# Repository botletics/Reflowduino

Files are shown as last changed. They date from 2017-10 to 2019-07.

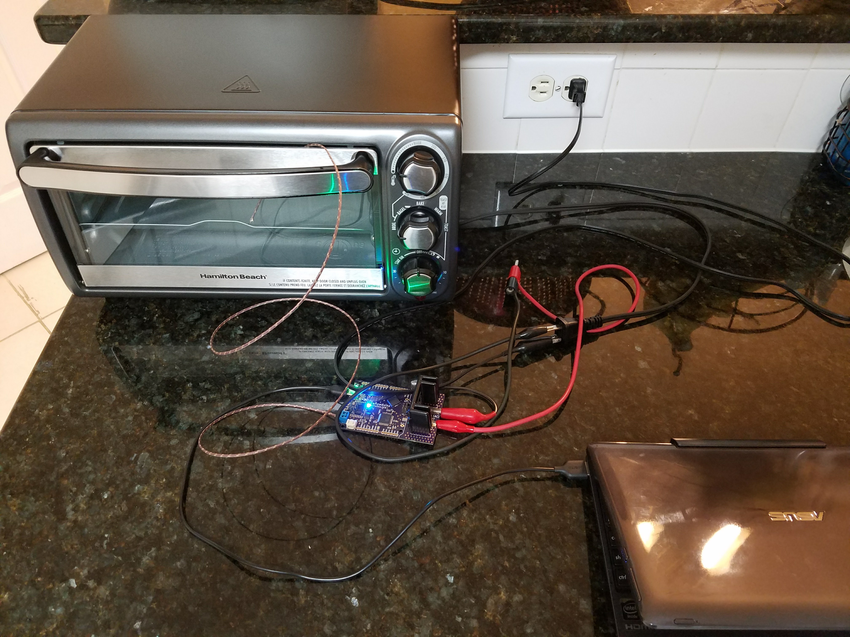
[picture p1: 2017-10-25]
Media/Toaster Oven Test Setup 1.jpg

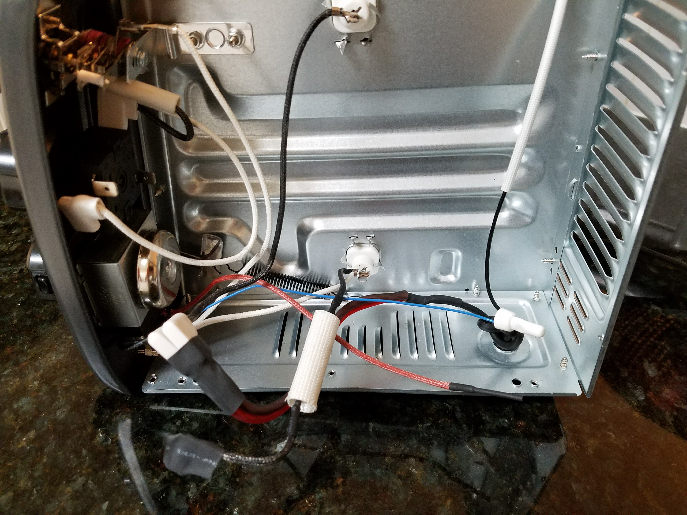
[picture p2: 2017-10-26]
Media/Toaster Oven Finished Wiring.jpg

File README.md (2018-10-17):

# Reflowduino

## Introduction
First off, let's briefly explain a circuit board is assembled. To aid in the explanation, let's take the analogy of baking a pizza. First of all you'll need the crust, which for us is a bare printed circuit board (PCB) made with different layers of a plastic substrate and copper traces that make the electrical connections. Next, we'll need the cheese that holds everything together, which for us is solder paste (yes, solder in the form of a paste) which "reflows" (solidifies or cures) at a high temperature. The solder paste is applied to the exposed copper pads on the PCB by way of a stencil that is aligned over the PCB. Then we'll grab some toppings, the electrical components, and place them in their appropriate locations on top of the solder paste. The final step is to bake our "pizza" so that the "cheese" holds all the components in place to yield our final assembled board! This is where the Reflowduino project comes in...

## Overview
The Reflowduino project is an entire do-it-yourself (DIY) reflow ecosystem consisting of open-source hardware specifically built to make it easy to control reflow appliances and apply PID temperature control while maintaining full flexibility in programming and usage while offering a bunch of features.

Since I'm a firm believer of great online resources having learned everything on my own aside from my Mechanical Engineering degree, I'm sharing all of this as completely open-source for everyone to enjoy, including EAGLE PCB files, Arduino IDE example code, sample Android app for Bluetooth control, and full tutorials on how to modify a toaster oven to start cookin’!

That being said, I do offer the boards listed below [for sale on my website](https://www.botletics.com/products/). Each order helps me out a little bit in creating and sharing new projects with everyone! :)

## Resources
Don’t forget to check out the [comprehensive Github wiki](https://github.com/botletics/Reflowdiuno/wiki)!
I also posted [this Instructable](https://www.instructables.com/id/Reflowduino-DIY-BLE-Reflow-Oven-Controller/) as a quick 'n dirty summary of everything here as well as on [Hackster.io](https://www.hackster.io/botletics/diy-reflow-oven-with-reflowduino-af0219)!

All PCB design files and hardware are released under the [Creative Commons Attribution Share Alike 4.0](https://choosealicense.com/licenses/cc-by-sa-4.0/) license.

All other software is released under the [GNU General Public License v3.0](https://choosealicense.com/licenses/gpl-3.0/).

## Safety Disclaimer
If you are a beginner in electronics or don't have the proper experience to work with mains voltage, I would suggest that you either don't mess with it, consult a professional, or keep learning until you're proficient enough! I am not liable for any mishaps that may occur due to misuse of the Reflowduino or its associated components or electrical system (including mains power). Take all safety precautions as necessary, such as gloves and certified safety glasses. Moreover, it is not recommended that you use the same appliance to reflow PCB's and also to cook food for consumption, which may result in food poisoning, especially with leaded solder. You are fully responsible for your actions, and perform them at your own risk!

That being said, DIY away my friends... have fun and stay safe!

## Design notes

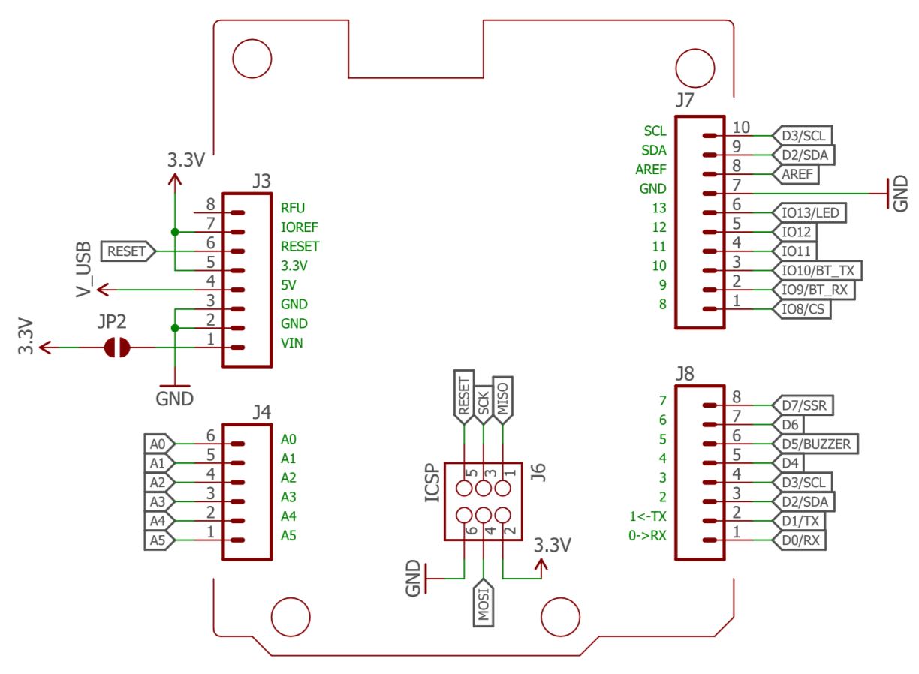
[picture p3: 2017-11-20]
Media/SchematicPinout.JPG

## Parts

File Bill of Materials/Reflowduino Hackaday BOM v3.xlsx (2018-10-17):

Part # | Part Description | Quantity | Notes | Mfg. Number
C1, C5 | 4.7uF/6.3V/10%/X5R Ceramic Capacitor 0603 | 2 |  | CL10A475KQ8NNNL
C2,C4,C8,C10 | 0.1uF/16V/20%/X7R Ceramic Capacitor 0603 | 4 |  | CL10B104MO8NNND
C3, C6, C7 | 1uF/25V/10%/X5R Ceramic Capacitor, 0603 | 3 |  | CL10A105KA8NNLC
C9 | 0.01uF/16V/10%/X7R Ceramic Capacitor 0603 | 1 |  | CL10B103KO8NNNC
D1 | Schottky Diode, 20V/1A, SOD-123FL | 1 |  | MBR120VLSFT3G
F1 | PTC Resettable Fuse, 750mA | 1 | 1210 package | 0ZCH0075AF2E
IC1 | Single Cell Li-Ion Charger IC, SOT23-5 | 1 |  | MCP73831T-2ACIOT
IC2 | ATMEGA32U4RC-AU, 44TQFP (10x10) | 1 | Internal calib. RC | ATMEGA32U4RC-AU
IC3 | 3.3V/600mA Regulator, SOT23-5 | 1 |  | AP2112K-3.3TRG1
IC4 | MAX31855 Thermocouple-to-Digital Converter | 1 | K-type | MAX31855KASA+
J1 | Micro USB Connector, SMT with Alignment Pins | 1
J2 | 2mm JST-PH SMT RA Connector | 1 |  | S2B-PH-SM4-TB(LF)(SN)
J3, J8 | 1x8 Female Header, 2.54mm Pitch/8.5mm Tall | 2
J4 | 1x6 Female Header, 2.54mm Pitch/8.5mm Tall | 1
J5 | 2-pin Screw Terminal Block, 3.5mm Pitch | 1 |  | T502015000J0G
J6 | 3x2 ICSP Male Header, 2.54mm Pitch | 1 |  | 54102-G08-00
J7 | 10x1 Female Header, 2.54mm Pitch/8.5mm Tall | 1
L1-L2 | 600Ohm Ferrite Bead, Signal Filter, 0603 | 2 |  | BLM18TG601TN1D
LED1-LED2 | 3.2V/20mA Green LED, 0603 | 2 |  | 150060GS75000
LED3 | 2V/20mA Red LED, 0603 | 1 |  | 150060RS75000
LED4 | 3.2V/20mA Blue LED, 0603 | 1 |  | 150060BS75000
Q1 | N-MOSFET, 200mA, SOT23-3 | 1 | Very low Vth | BSS138L
R1, R3 | 2k/1%/0.1W Resistor 0603 | 2 |  | ERJ-3GEYJ202V
R2, R4 | 22/5%/0.1W Resistor 0603 | 2 |  | RC1608J220CS
R5,R9,R10 | 10k/5%/0.1W Resistor 0603 | 3 |  | NRC06J103TRF
R6-R7 | 4.02k/1%/0.1W Resistor 0603 | 2 |  | RK73H1JTTD4021F
R8, R11 | 470/5%/0.1W Resistor 0603 | 2 |  | RMCF0603JT470R
RY1 | Opto-Isolated Solid State Relay | 1 | 25A/280V max | SPF240D25
SPK1 | Piezo Buzzer, 65dB | 1 |  | PKMCS0909E4000-R1
SW1 | Pushbutton Switch, SPST-NO, 300gf/2.5mm Tall | 1 |  | KMR731NGLFS
U1 | HM-11 Bluetooth SMD Module | 1
Y1 | 8MHz Resonator | 1 |  | CSTCE8M00G52-R0
 | K-type Thermocouple, Glass Braid Insulation | 1 |  | 240-080

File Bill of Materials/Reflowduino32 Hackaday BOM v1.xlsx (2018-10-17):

Part # | Part Name | Quantity | Notes | Mfg. Number
C1 | 0.1uF/16V/20%/X7R Ceramic Capacitor 0603 | 1 |  | CL10B104MO8NNND
C2 | 0.01uF/16V/10%/X7R Ceramic Capacitor 0603 | 1 |  | CL10B103KO8NNNC
IC1 | MAX31855 Thermocouple-to-Digital Converter | 1 | K-type | MAX31855KASA+
J1, J3 | 1x6 Female Header, 2.54mm Pitch/8.5mm Tall | 2
J5-J6 | 2-pin Screw Terminal Block, 3.5mm Pitch | 2 |  | T502015000J0G
L1-L2 | 600Ohm Ferrite Bead, Signal Filter, 0603 | 2 |  | BLM18TG601TN1D
Q1 | N-MOSFET, 200mA, SOT23-3 | 1 | Very low Vth | BSS138L
R1-R2 | 10k/5%/0.1W Resistor 0603 | 2 |  | NRC06J103TRF

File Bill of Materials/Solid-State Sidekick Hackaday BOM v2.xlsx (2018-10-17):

Part # | Part Description | Quantity | Notes | Mfr. Number
J1 | C14 Entry Conn Receptacle, Right Angle | 1 |  | 703W-00/53
J2 | AC Receptacle | 1 |  | 3-213598-2
J3 | 2-pin Screw Terminal Block, 3.5mm Pitch | 1 |  | T502015000J0G
RY1 | Opto-Isolated Solid State Relay | 1 | 25A/280V max | SPF240D25
SW1 | SPST ON-OFF Rocker Switch, Right Angle | 1 | 15A/125VAC | R1966ABLKBLKFR

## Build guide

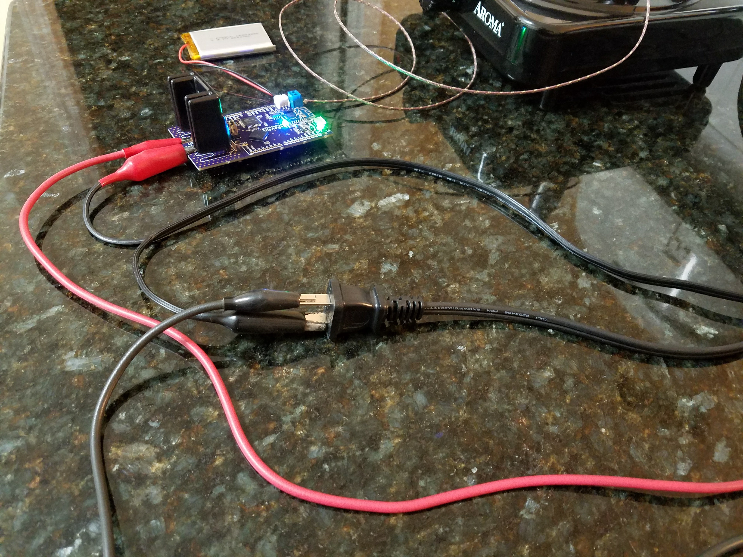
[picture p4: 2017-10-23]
Media/Hot Plate Demo Setup Closeup.jpg

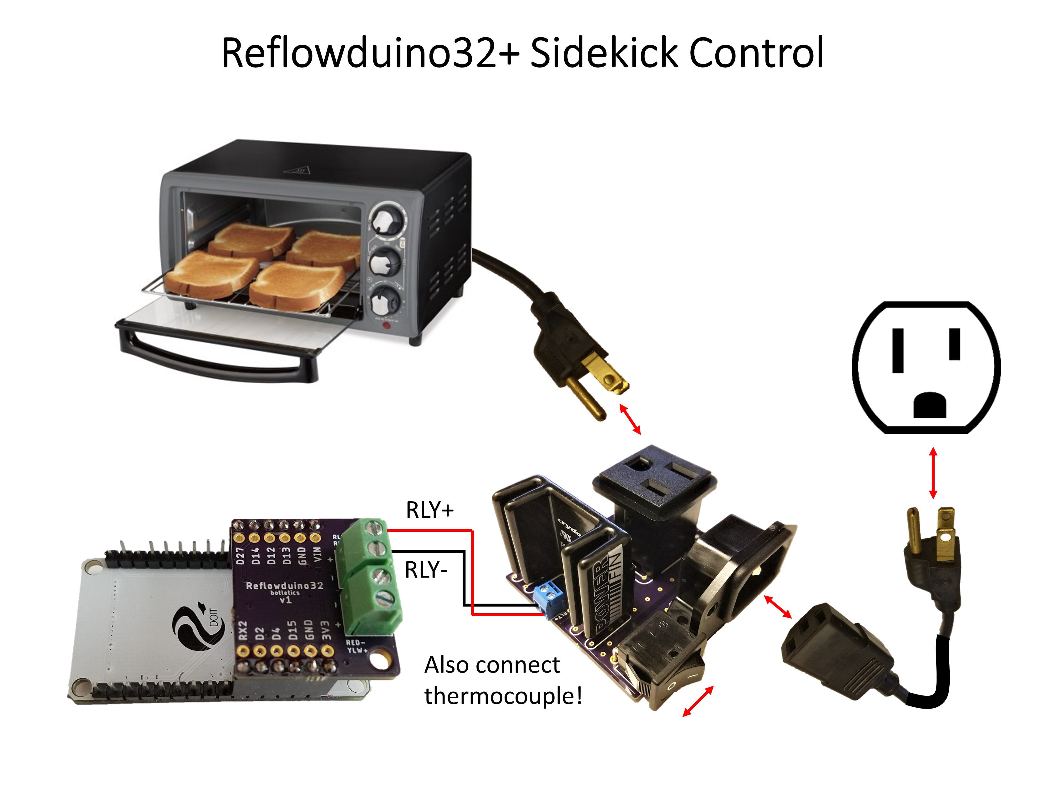
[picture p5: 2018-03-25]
Media/Reflowduino32 + Sidekick Wiring.jpg

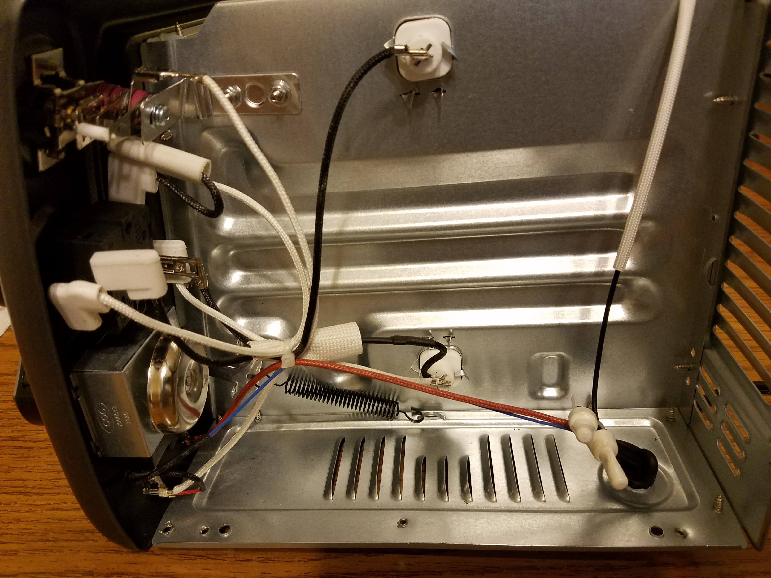
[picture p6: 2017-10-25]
Media/Toaster Oven Original Wiring.jpg

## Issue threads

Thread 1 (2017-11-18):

Include documentation for adding ESP32 functionality and standalone displays

vogelfreiheit, 2017-11-18:
I think adding some documentation for adding ESP32 modules and standalone displays would be great. There should be enough IO pins left for both, AFAIK.

botletics, 2017-11-20:
Hi there, thanks for the suggestion! Sorry I didn't see this earlier. Adding support for display shields is currently in the [to-do list](https://github.com/botletics/Reflowduino/wiki/To-Do-List) and ESP32 support sounds fun! I'll keep you updated when that happens. In the meantime I'm launching an Indiegogo campaign for Reflowduino on December 1st!

VinnyCordeiro, 2017-11-20:
There was a project of a reflow oven called [Reflow Château](https://hackaday.com/2015/02/02/reflow-chateau/) that appeared in 2015 on Hackaday that uses a Teensy 3.1 and a graphic touchscreen display. The original website of the project is down but there is a copy of it here on Github. I've made [a fork of it](https://github.com/VinnyCordeiro/ReflowChateau), as there are some missing files in the original repo.

The controller works but uses obsolete/discontinued components, namely the thermocouple IC and the solid-state relays. I had the idea to update the project, but never had the time to really do that. I hope that this project will help to improve yours. The original project uses the Apache License, so it's open source.

botletics, 2017-11-20:
Awesome, thanks! I'll check it out when I get a chance.

vogelfreiheit, 2017-12-16:
I might be able to work on this soon, just got a Xmas sized lot of components and boards that are too much of a PITA to do without a reflow oven.

botletics, 2017-12-19:
I'm working on making an Instructables tutorial and YouTube video about how to build a BLE Android app for the ESP32. Stay tuned! Maybe I could also build a custom PCB that uses the ESP32 dev board as the controller that snaps into some headers?!?!

tedder, 2018-01-09:
esp32? ooo. I've been modding my 'duino and figure I'll switch to an esp32, perhaps a wemos-with-OLED one. hmm.

botletics, 2018-01-09:
Haha yea that would have to be a completely separate board but it's doable. Just a matter of when I can find time for such things  :)

tedder, 2018-01-09:
Right, it'll replace the 32u4. No reason to interface with it. I'm just glad to see others may be interested in it.

botletics, 2018-03-24:
Just added ESP32 support! I made a "backpack" module for this [DOIT ESP32 dev board](https://www.amazon.com/Docreate-Development-Bluetooth-Ultra-Low-Consumption/dp/B0754DT83W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).

Closed 2018-03-24.

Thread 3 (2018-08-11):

Use of a Halogen Floodlight as Reflow Oven

Reaper2u, 2018-08-11:
Hello botletics

I am using the ESP32 Version to try to drive a Halogen Floodlight as a mini Reflow Oven. Most important point for me is, that I can easily take it with me, should I need to.

My problem with that approach is, that it is way too fast. I basically get no soak phase, as the Halogen Floodlight heats up so quick. The whole process until it reaches the peak temperature takes about 30 seconds, which is way too short.

Is there a chance You can test that, and maybe give me a hint what I can do to actually have useable soak and reflow phases?

Thanks in advance.

Best regards

Reaper2u

botletics, 2018-08-11:
Sorry, I don't have the time and I am not interested in testing that. Best of luck with your project though.

tedder, 2018-08-16:
@Reaper2u, what you need to do is tune [the pid parameters](https://github.com/botletics/Reflowduino/blob/master/Example%20Code/Reflowduino_Demo/Reflowduino_Demo.ino#L91) to account for the rate difference. I built a new board and wrote code from scratch to control my reflowduino (okay, so, not much left of it at that point). [Here are some good overviews of pid and how to tune it.](https://pinboard.in/u:tedder42/t:pid/)

Closed 2018-08-11.

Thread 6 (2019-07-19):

Reflowduino32: Relay not being triggered

Jizanthapus, 2019-07-19:
I've assembled the Reflowduino32 and Sidekick module and connected them to my toaster oven. However, when I start a reflow sequence the toaster oven does not receive power.

I modified the simple blink program to test whether the Sidekick and ESP32 backpack modules were working:
```
#define relay 13

// the setup function runs once when you press reset or power the board
void setup() {
  // initialize digital pin LED_BUILTIN as an output.
  pinMode(LED_BUILTIN, OUTPUT);
  pinMode(relay, OUTPUT);
}

// the loop function runs over and over again forever
void loop() {
  digitalWrite(LED_BUILTIN, HIGH);   // turn the LED on (HIGH is the voltage level)
  digitalWrite(relay, HIGH);
  delay(3000);                       // wait for a second
  digitalWrite(LED_BUILTIN, LOW);    // turn the LED off by making the voltage LOW
  digitalWrite(relay, LOW);
  delay(3000);                       // wait for a second
}
```

This code works fine and I can see my oven come on and go off with the built in LED.

When I flash back to the Reflowduino_ESP32_Demo code, nothing happens with the oven. The Bluetooth connection and thermocouple reporting work fine. While measuring pin 13 with a voltmeter, I do not see it go high while the process is running.

It's possible that I've overlooked something very simple, but I can't think of anything off the top of my head.

Thanks

botletics, 2019-07-19:
Did you start the reflow process with the Android app via Bluetooth?

Jizanthapus, 2019-07-19:
Yes. I hit "Start" and the blue LED came on but the oven did not.

botletics, 2019-07-20:
The oven will only turn on when the *red* LED on the Reflowduino board turns on. The blue LED when solidly lit means it's connected via Bluetooth. Perhaps I'll have to look into the app. In the serial monitor do you see the command from the app's START button being sent to the ESP32?

Jizanthapus, 2019-07-20:
When I plug the ESP in, I get a red LED and serial output showing the temperature. After hitting START on the Android app, the blue LED comes on and I see serial output stating that the reflow process has begun. I also get the reported temperature displayed and graphed in the app. No relay activation. After hitting STOP in the app, I the blue LED turns off and I get serial output stating that the reflow process has been aborted.

Today though I had a slight bug with the Android app. When I hit the start button, it said that there was a runtime error in the app and it closed. Restarting the app allowed me to continue as normal. As it doesn't happen every time I hit START, I don't think this is related to the relay not functioning, but I thought I'd mention it anyway.

I hooked the backpack's power and SPI pins up to the ESP and routed pin 13 solely to an o-scope. I never saw that pin flicker when hitting START on the Android app.

botletics, 2019-07-20:
Pin 13 is the red LED. Pin 7 controls the relay per [this wiki page](https://github.com/botletics/Reflowduino/wiki/Pinouts). I'll look into it more when I get a chance, thanks for the heads up.

Jizanthapus, 2019-07-20:
I'm using the Reflowduino32 backpack for the ESP32 board. According to the [schematic](https://github.com/botletics/Reflowduino/blob/master/Schematics/Reflowduino32%20Backpack%20Schematic%20v1.png) and [code,](https://github.com/botletics/Reflowduino/blob/master/Example%20Code/Reflowduino_ESP32_Demo/Reflowduino_ESP32_Demo.ino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) pin 13 drives the MOSFET that activates the SSR controlling the oven.

botletics, 2019-07-20:
Oh sorry, I was looking at the wrong thing, thank you.

botletics, 2019-07-20:
Could you please screenshot what you see in the serial monitor? Thanks.

Jizanthapus, 2019-07-21:
Haha, no worries

I did a little more testing today...

It appears that line [316](https://github.com/botletics/Reflowduino/blob/master/Example%20Code/Reflowduino_ESP32_Demo/Reflowduino_ESP32_Demo.ino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) is where you are turning on the relay. So I added a little serial output there:
```
if (output > millis() - windowStartTime) {
      digitalWrite(relay, HIGH); // If HIGH turns on the relay
      Serial.println("Activated Relay");
      }
```

After starting the reflow process from the app, I never saw that output. I do get the `<-- ***Reflow process started!` from line [164](https://github.com/botletics/Reflowduino/blob/master/Example%20Code/Reflowduino_ESP32_Demo/Reflowduino_ESP32_Demo.ino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).

Jizanthapus, 2019-07-21:
[Here is the serial output](https://gist.github.com/Jizanthapus/48d9e5a6e959edf510303ae55729ed68) from my modified code

botletics, 2019-07-22:
So it looks like the app and Bluetooth is working but the relay isn't turning on? Weird. What are your settings for T_preheat, T_soak, and T_reflow on lines 81-83 in the Reflowduino_ESP32_Demo?

Jizanthapus, 2019-07-22:
Yes, yes, and I haven't changed them from the ones you provide (I am planning on using a low-temp lead-free solder paste).

The only modification to your code that I've made is inserting the serial output where the relay is supposed to go HIGH.

botletics, 2019-07-22:
So the only thing I can think of that could be the culprit is that I divided the preheat_rate, soak_rate, reflow_rate, and cool_rate variables by 1000 in lines 263, 276, 288, and 304 because of [this issue](https://github.com/botletics/Reflowduino/issues/5) but I haven't tested that yet. Could you try deleting the "/ 1000" part and see if it at least runs?

botletics, 2019-07-22:
Also, if you try the [PID_Test](https://github.com/botletics/Reflowduino/blob/master/Example%20Code/PID_Test/PID_Test.ino) it should turn the oven on.

Jizanthapus, 2019-07-23:
I tried PID_Test (with some [modifications](https://gist.github.com/Jizanthapus/fa0ab96277080cf2d81ee36eaa1868aa) for the ESP32) and removing the "/ 1000" in the Demo code. Both resulted in Pin 13 going HIGH on the START command.

I think you are correct about the culprit.

botletics, 2019-07-23:
Hmmm OK. What if you change the " / 1000" to " / 1000.0" to make sure it's doing the math properly?

Jizanthapus, 2019-07-23:
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

It works!
Does that profile look about right to you?

botletics, 2019-07-23:
Ehhh it looks a little like a camel but it's approximately right. Maybe the PID needs some tuning. Did it work when you added the "1000.0" decimal place?

Jizanthapus, 2019-07-24:
Yep. That did the trick.

Based on the wiki and my results, I'm thinking maybe I need to tweak my derivative gain to counter some of that overshoot. Does that sound reasonable or am I misunderstanding the PID parameters?

Since it's working now, I'll go ahead and close the issue. Thanks for all your help!

botletics, 2019-07-24:
Great, thanks for letting me know.

I think you should lower Kp and increase Kd a little but not too much. Protip: What you could do for testing is lower the preheat/soak/reflow temperatures so you don't have to wait for it to heat all the way up every time.

Closed 2019-07-24.

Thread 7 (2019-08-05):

About ESP32 Bluetooth lib.

icebabycool, 2019-08-05:
Hi there botletics, i`ve been try your ESP32 version code for do it on my own, but i can`t find some libraries that you used in ESP32.ino, they are:
#include <BLEDevice.h>
#include <BLEServer.h>
#include <BLEUtils.h>
#include <BLE2902.h>

So may i ask you to addd these in to the project folder? Thanks!

botletics, 2019-08-05:
Please see [this wiki page](https://github.com/botletics/Reflowduino/wiki/ESP32-Arduino-Setup)

Closed 2019-08-05.

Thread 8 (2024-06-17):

arduino complaining about conversion from string to non-scalar type std::string {aka 'std::__cxx11::basic_string<char>'} requested

NormalHuman-Anything, 2024-06-17:
wanted to build a reflow oven so found this code that runs on esp32 and tried compiling it, only to find out i met with a error
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

Closed 2024-06-20.

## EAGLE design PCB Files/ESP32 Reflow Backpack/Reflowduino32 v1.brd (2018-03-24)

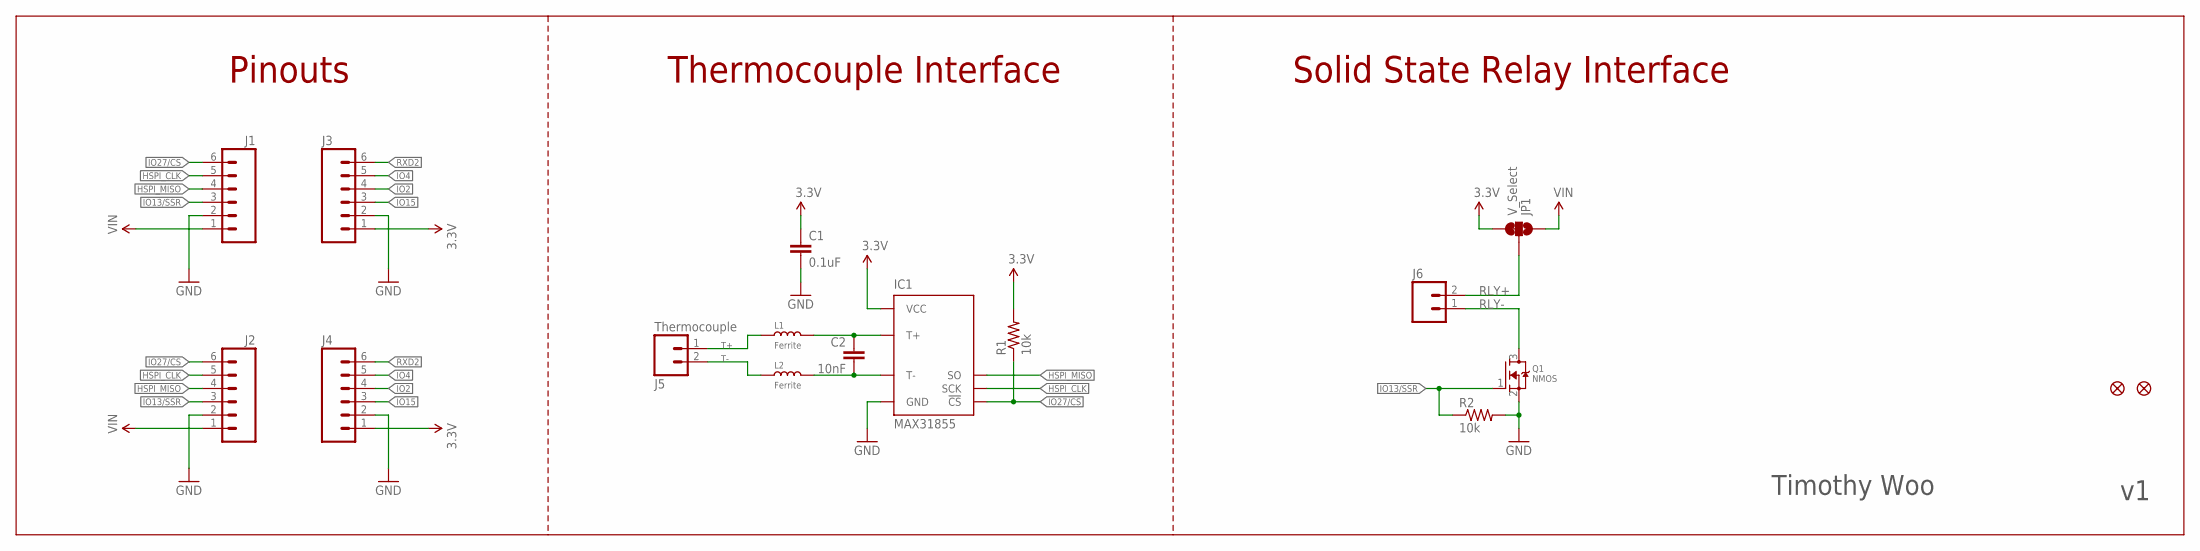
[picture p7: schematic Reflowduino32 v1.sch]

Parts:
C1: 0.1uF; 0603-CAP-MARKED
C2: 10nF; 0603-CAP-MARKED
FID1, FID2: FIDUCIAL; FIDUCIAL_1MM
IC1: MAX31855; MAX31855_SOIC8
J1, J3: M06SILK_PTH; 1X06
J2, J4: M06NO_SILK_FEMALE_PTH; 1X06_NO_SILK
J5: Thermocouple; SCREWTERMINAL-3.5MM-2
J6: M023.5MM; SCREWTERMINAL-3.5MM-2
JP1: V_Select; SMT-JUMPER_3_1-NC_TRACE_SILK
L1, L2: Ferrite; L0603
Q1: NMOS; SOT23-3
R1, R2: 10k; 0603-RES-MARKED

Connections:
3.3V: C1.1, IC1.4 (VCC), J3.1, J4.1, JP1.3, R1.2
GND: C1.2, IC1.1 (GND), J1.2, J2.2, J3.2, J4.2, Q1.2 (S), R2.2
HSPI_CLK: IC1.5 (SCK), J1.5, J2.5
HSPI_MISO: IC1.7 (SO), J1.4, J2.4
IO2: J3.4, J4.4
IO4: J3.5, J4.5
IO13/SSR: J1.3, J2.3, Q1.1 (G), R2.1
IO15: J3.3, J4.3
IO27/CS: IC1.6 (!CS), J1.6, J2.6, R1.1
unnamed: C2.2, IC1.2 (T-), L2.2
unnamed: C2.1, IC1.3 (T+), L1.2
RLY+: J6.2, JP1.2
RLY-: J6.1, Q1.3 (D)
RXD2: J3.6, J4.6
T+: J5.1, L1.1
T-: J5.2, L2.1
VIN: J1.1, J2.1, JP1.1

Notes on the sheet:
Thermocouple Interface
Solid State Relay Interface
Pinouts
Timothy Woo

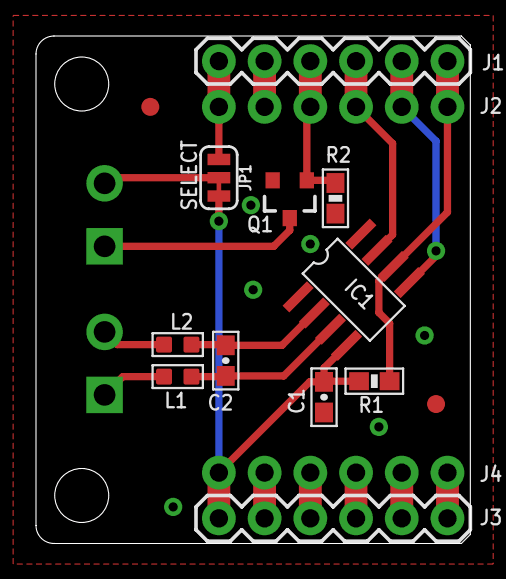
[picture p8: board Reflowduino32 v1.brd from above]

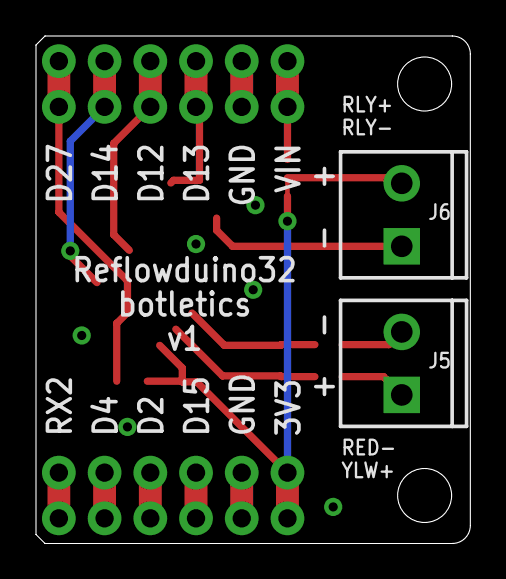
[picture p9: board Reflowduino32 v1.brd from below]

Board: 2 copper layers, 24.1 x 28.2 mm, 17 parts (2 on the bottom side), 17 nets.

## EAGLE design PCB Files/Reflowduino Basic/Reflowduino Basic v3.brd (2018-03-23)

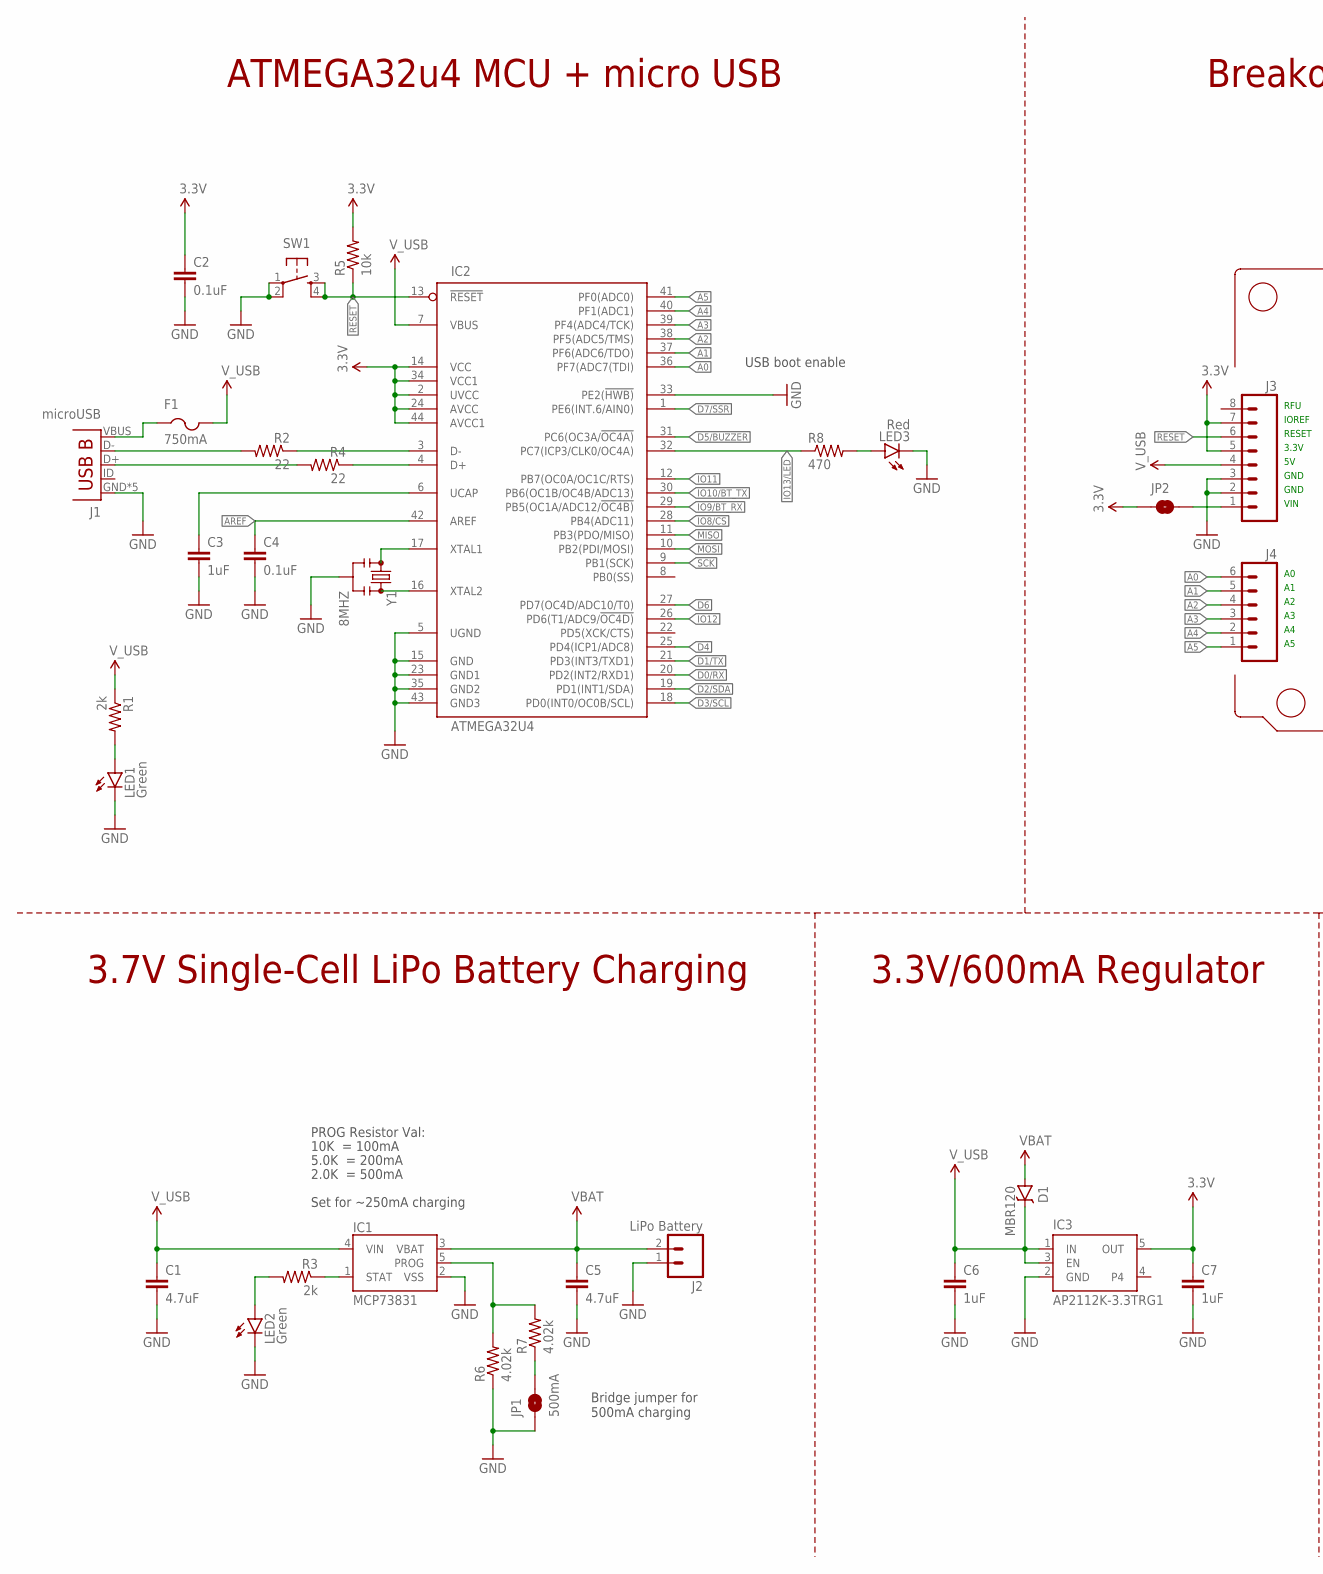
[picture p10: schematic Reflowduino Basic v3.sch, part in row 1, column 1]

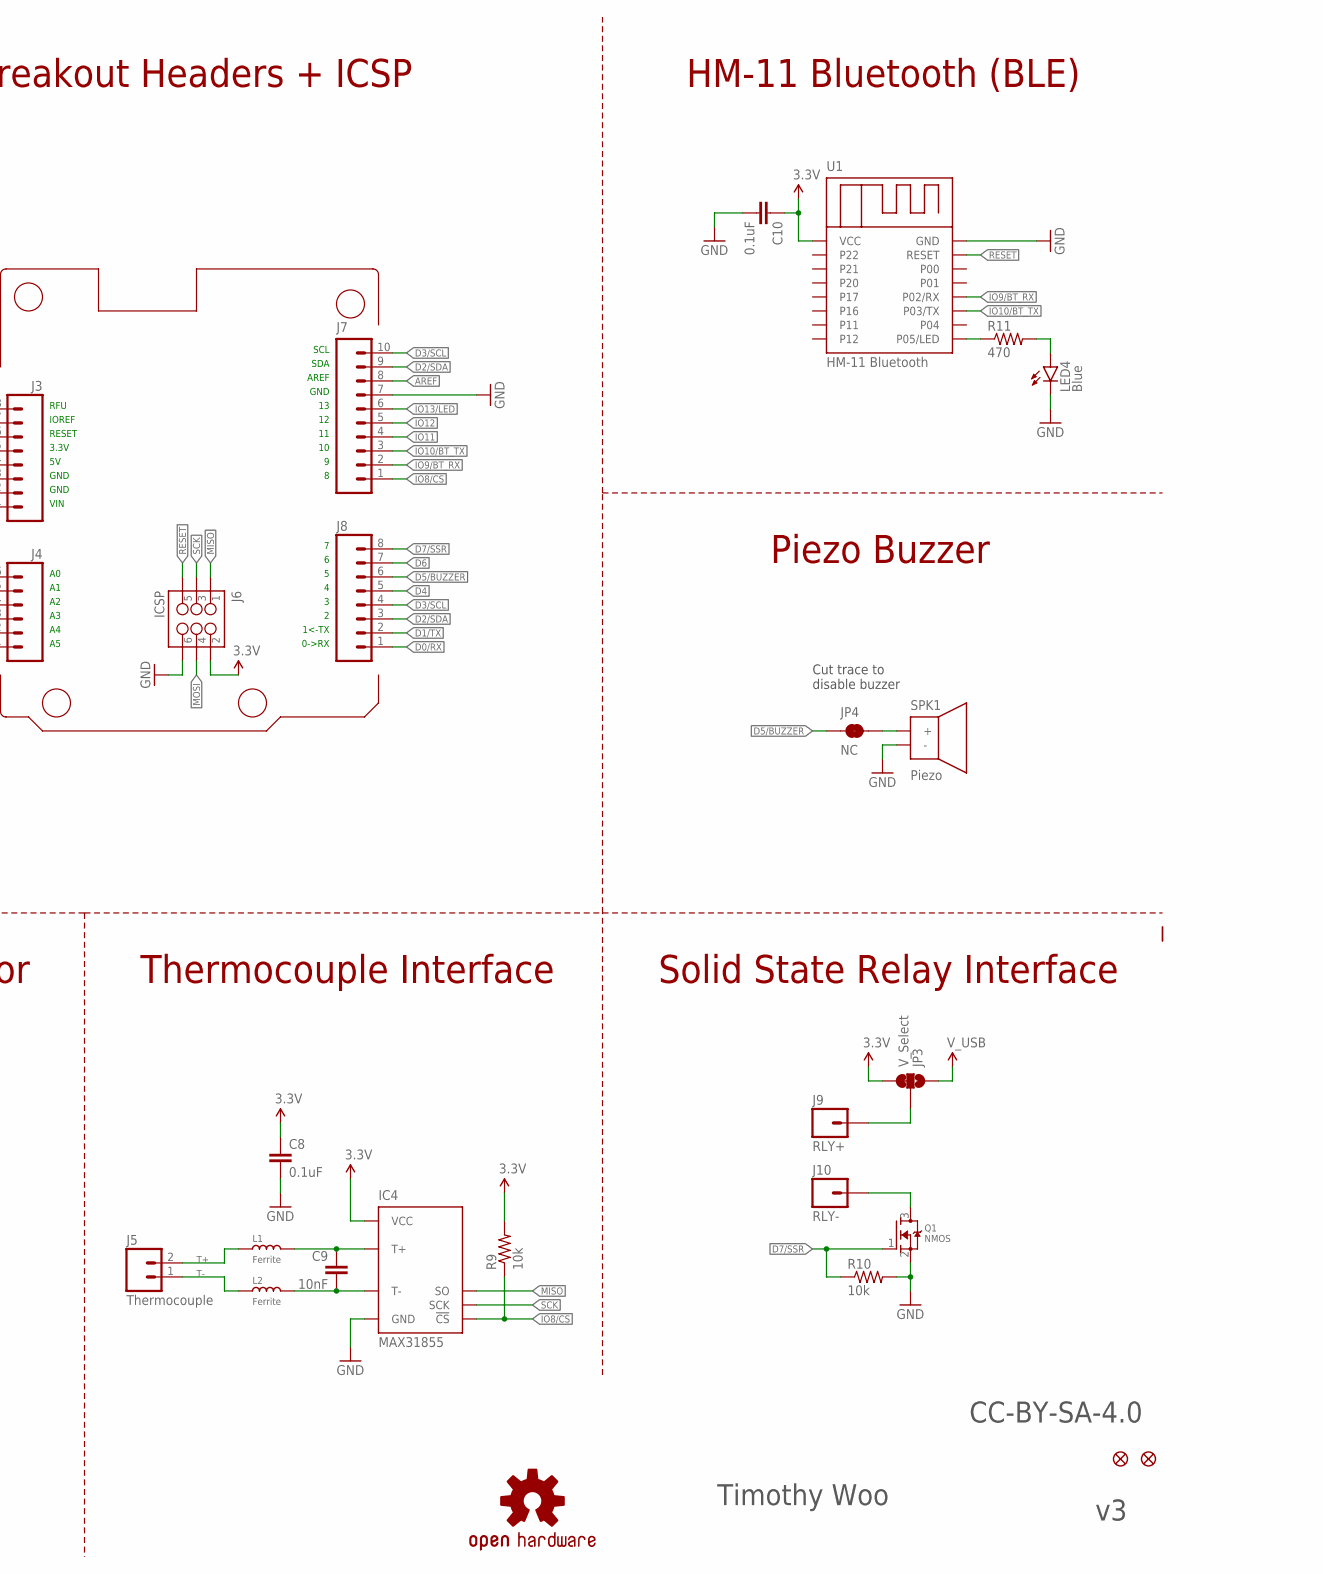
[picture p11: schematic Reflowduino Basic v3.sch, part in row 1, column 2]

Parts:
C1, C5: 4.7uF; 0603-CAP-MARKED
C2, C4, C8, C10: 0.1uF; 0603-CAP-MARKED
C3, C6, C7: 1uF; 0603-CAP-MARKED
C9: 10nF; 0603-CAP-MARKED
D1: MBR120; SOD-123FL
F1: 750mA; 1210
FID1, FID2: FIDUCIAL; FIDUCIAL_1MM
IC1: MCP73831; SOT23-5
IC2: ATMEGA32U4; TQFP44
IC3: AP2112K-3.3TRG1; SOT23-5
IC4: MAX31855; MAX31855_SOIC8
J1: microUSB; USB-B-MICRO-SMD
J2: LiPo Battery; JST-2-SMD
J3, J8: M08SILK_PTH; 1X08
J4: M06SILK_PTH; 1X06
J5: Thermocouple; SCREWTERMINAL-3.5MM-2
J6: ICSP; 2X3
J7: M10SILK_PTH; 1X10
J9: RLY+; 1X01_LONGPAD
J10: RLY-; 1X01_LONGPAD
JP1: 500mA; SMT-JUMPER_2_NO_SILK
JP2: JUMPER-SMT_2_NO_SILK; SMT-JUMPER_2_NO_SILK
JP3: V_Select; SMT-JUMPER_3_1-NC_TRACE_SILK
JP4: NC; SMT-JUMPER_2_NC_TRACE_SILK
L1, L2: Ferrite; L0603
LED1, LED2: Green; LED-0603-MARKED
LED3: Red; LED-0603-MARKED
LED4: Blue; LED-0603-MARKED
LOGO1: OSHW-LOGOL; OSHW-LOGO-L
Q1: NMOS; SOT23-3
R1, R3: 2k; 0603-RES-MARKED
R2, R4: 22; 0603-RES-MARKED
R5, R9, R10: 10k; 0603-RES-MARKED
R6, R7: 4.02k; 0603-RES-MARKED
R8, R11: 470; 0603-RES-MARKED
SPK1: Piezo; BUZZER_PKMCS0909E4000
SW1: SWITCH_MOMENTARY_SPST_4-PINRECT; TACTILE_SWITCH_SMD_4.6X2.8MM
U1: HM-11 Bluetooth; JDY-08_BLUETOOTH
Y1: 8MHZ; CSTCE_RESONATOR_SMD

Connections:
3.3V: C2.1, C7.1, C8.1, C10.1, IC2.2 (UVCC), IC2.14 (VCC), IC2.24 (AVCC), IC2.34 (VCC1), IC2.44 (AVCC1), IC3.5 (OUT), IC4.4 (VCC), J3.5, J3.7, J6.2, JP2.1, JP3.3, R5.2, R9.2, U1.1 (VCC)
A0: IC2.36 (PF7(ADC7(TDI)), J4.6
A1: IC2.37 (PF6(ADC6/TDO)), J4.5
A2: IC2.38 (PF5(ADC5/TMS)), J4.4
A3: IC2.39 (PF4(ADC4/TCK)), J4.3
A4: IC2.40 (PF1(ADC1)), J4.2
A5: IC2.41 (PF0(ADC0)), J4.1
AREF: C4.1, IC2.42 (AREF), J7.8
D0/RX: IC2.20 (PD2(INT2/RXD1)), J8.1
D1/TX: IC2.21 (PD3(INT3/TXD1)), J8.2
D2/SDA: IC2.19 (PD1(INT1/SDA)), J7.9, J8.3
D3/SCL: IC2.18 (PD0(INT0/OC0B/SCL)), J7.10, J8.4
D4: IC2.25 (PD4(ICP1/ADC8)), J8.5
D5/BUZZER: IC2.31 (PC6(OC3A/!OC4A)), J8.6, JP4.1
D6: IC2.27 (PD7(OC4D/ADC10/T0)), J8.7
D7/SSR: IC2.1 (PE6(INT.6/AIN0)), J8.8, Q1.1 (G), R10.1
D+: IC2.4 (D+), R4.1
D-: IC2.3 (D-), R2.1
DC+: J9.1, JP3.2
DC-: J10.1, Q1.3 (D)
GND: C1.2, C2.2, C3.2, C4.2, C5.2, C6.2, C7.2, C8.2, C10.2, IC1.2 (VSS), IC2.5 (UGND), IC2.15 (GND), IC2.23 (GND1), IC2.33 (PE2(!HWB)), IC2.35 (GND2), IC2.43 (GND3), IC3.2 (GND), IC4.1 (GND), J1.GND, J1.SHIELD1 (GND), J1.SHIELD2 (GND), J1.SHIELD3 (GND), J1.SHIELD4 (GND), J2.1 (2), J3.2, J3.3, J6.6, J7.7, JP1.1, LED1.C, LED2.C, LED3.C, LED4.C, Q1.2 (S), R6.1, R10.2, SPK1.2 (-), SW1.1, SW1.2, U1.16 (GND), Y1.2
IO8/CS: IC2.28 (PB4(ADC11)), IC4.6 (!CS), J7.1, R9.1
IO9/BT_RX: IC2.29 (PB5(OC1A/ADC12/!OC4B)), J7.2, U1.12 (P02/RX)
IO10/BT_TX: IC2.30 (PB6(OC1B/OC4B/ADC13)), J7.3, U1.11 (P03/TX)
IO11: IC2.12 (PB7(OC0A/OC1C/RTS)), J7.4
IO12: IC2.26 (PD6(T1/ADC9/!OC4D)), J7.5
IO13/LED: IC2.32 (PC7(ICP3/CLK0/OC4A)), J7.6, R8.1
LED: R11.1, U1.9 (P05/LED)
MISO: IC2.11 (PB3(PDO/MISO)), IC4.7 (SO), J6.1
MOSI: IC2.10 (PB2(PDI/MOSI)), J6.4
unnamed: IC2.17 (XTAL1), Y1.1
unnamed: J1.D-, R2.2
unnamed: J1.D+, R4.2
unnamed: JP4.2, SPK1.1 (+)
unnamed: LED2.A, R3.2
unnamed: C9.2, IC4.2 (T-), L2.2
unnamed: C9.1, IC4.3 (T+), L1.2
unnamed: LED1.A, R1.2
unnamed: IC2.16 (XTAL2), Y1.3
unnamed: LED4.A, R11.2
unnamed: JP1.2, R7.1
unnamed: J3.1, JP2.2
unnamed: LED3.A, R8.2
PROG: IC1.5 (PROG), R6.2, R7.2
RESET: IC2.13 (!RESET), J3.6, J6.5, R5.1, SW1.3, SW1.4, U1.15 (RESET)
SCK: IC2.9 (PB1(SCK)), IC4.5 (SCK), J6.3
STAT: IC1.1 (STAT), R3.1
T+: J5.2, L1.1
T-: J5.1, L2.1
UCAP: C3.1, IC2.6 (UCAP)
VBAT: C5.1, D1.A, IC1.3 (VBAT), J2.2 (1)
V_USB: C1.1, C6.1, D1.C, F1.2, IC1.4 (VIN), IC2.7 (VBUS), IC3.1 (IN), IC3.3 (EN), J3.4, JP3.1, R1.1
XUSB: F1.1, J1.VBUS

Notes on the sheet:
Timothy Woo
IOREF
RFU
3.3V
RESET
GND
VIN
0->RX
1<-TX
AREF
SDA
SCL
Set for ~250mA charging
10K = 100mA
5.0K = 200mA
2.0K = 500mA
PROG Resistor Val:
ATMEGA32u4 MCU + micro USB
3.7V Single-Cell LiPo Battery Charging
3.3V/600mA Regulator
Breakout Headers + ICSP
HM-11 Bluetooth (BLE)
Solid State Relay Interface
Thermocouple Interface
Piezo Buzzer
Bridge jumper for 500mA charging
Cut trace to disable buzzer
USB boot enable
CC-BY-SA-4.0

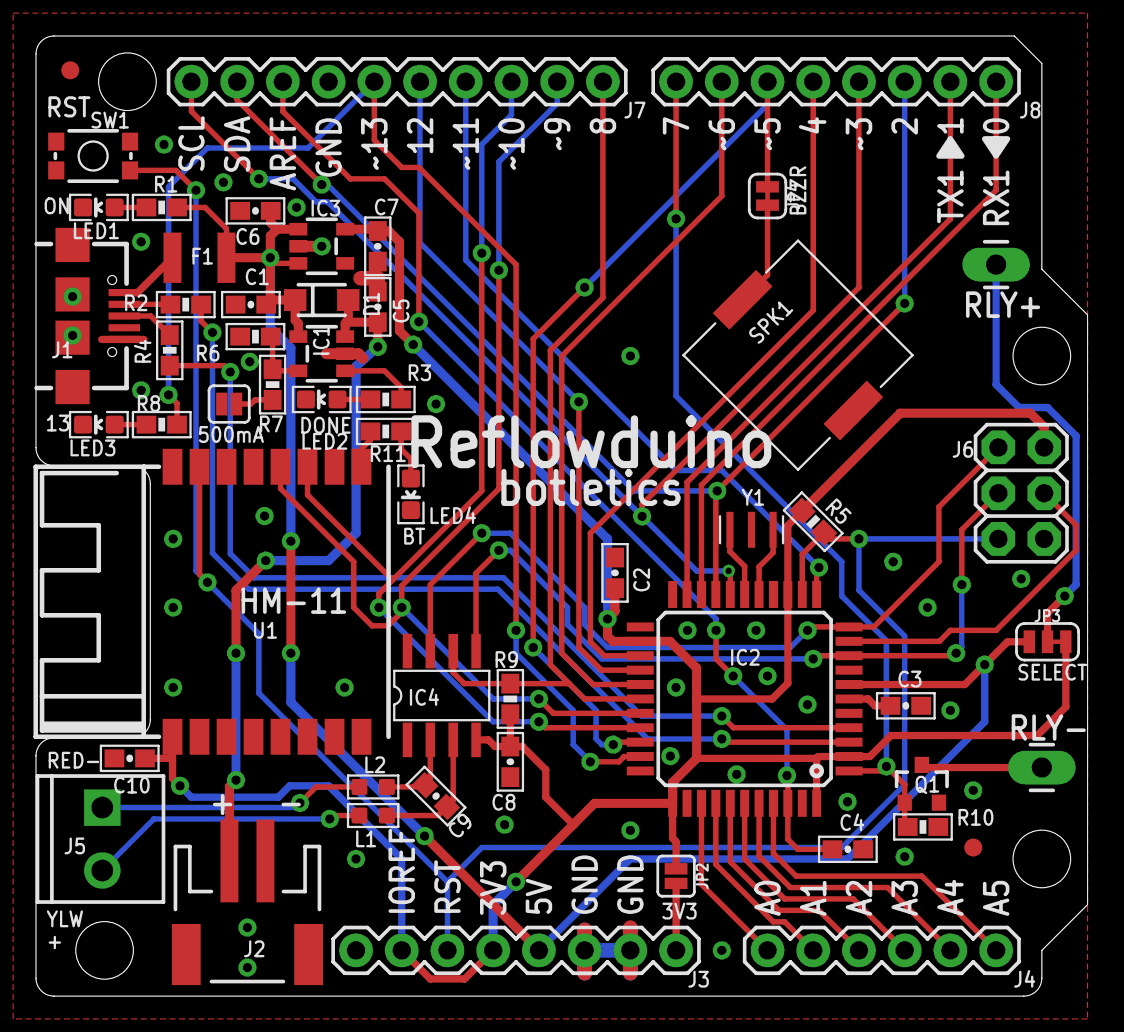
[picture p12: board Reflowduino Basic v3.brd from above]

Board: 2 copper layers, 58.4 x 53.3 mm, 55 parts (1 on the bottom side), 53 nets.

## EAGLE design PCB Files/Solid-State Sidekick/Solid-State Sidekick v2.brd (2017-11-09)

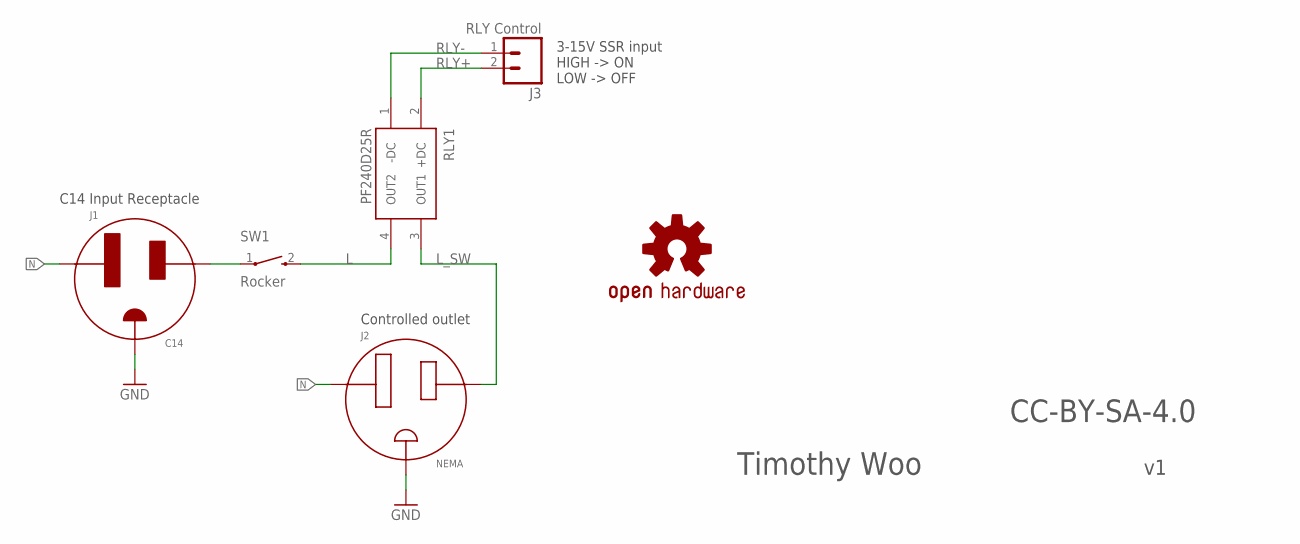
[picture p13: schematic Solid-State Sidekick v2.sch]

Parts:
J1: C14; 703W-00/53
J2: NEMA; 3-213598-2
J3: RLY Control; SCREWTERMINAL-3.5MM-2
LOGO1: OSHW-LOGOL; OSHW-LOGO-L
RLY1: PF240D25R; RELAY_PF240
SW1: Rocker; R1966ABLKBLKFR

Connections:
GND: J1.E, J2.GND (E)
L: RLY1.4 (OUT2), SW1.2
L_SW: J2.L, RLY1.3 (OUT1)
L_WALL: J1.L, SW1.1
N: J1.N, J2.N
RLY+: J3.2, RLY1.2 (+DC)
RLY-: J3.1, RLY1.1 (-DC)

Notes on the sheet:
Controlled outlet
3-15V SSR input HIGH -> ON LOW -> OFF
C14 Input Receptacle
Timothy Woo
CC-BY-SA-4.0

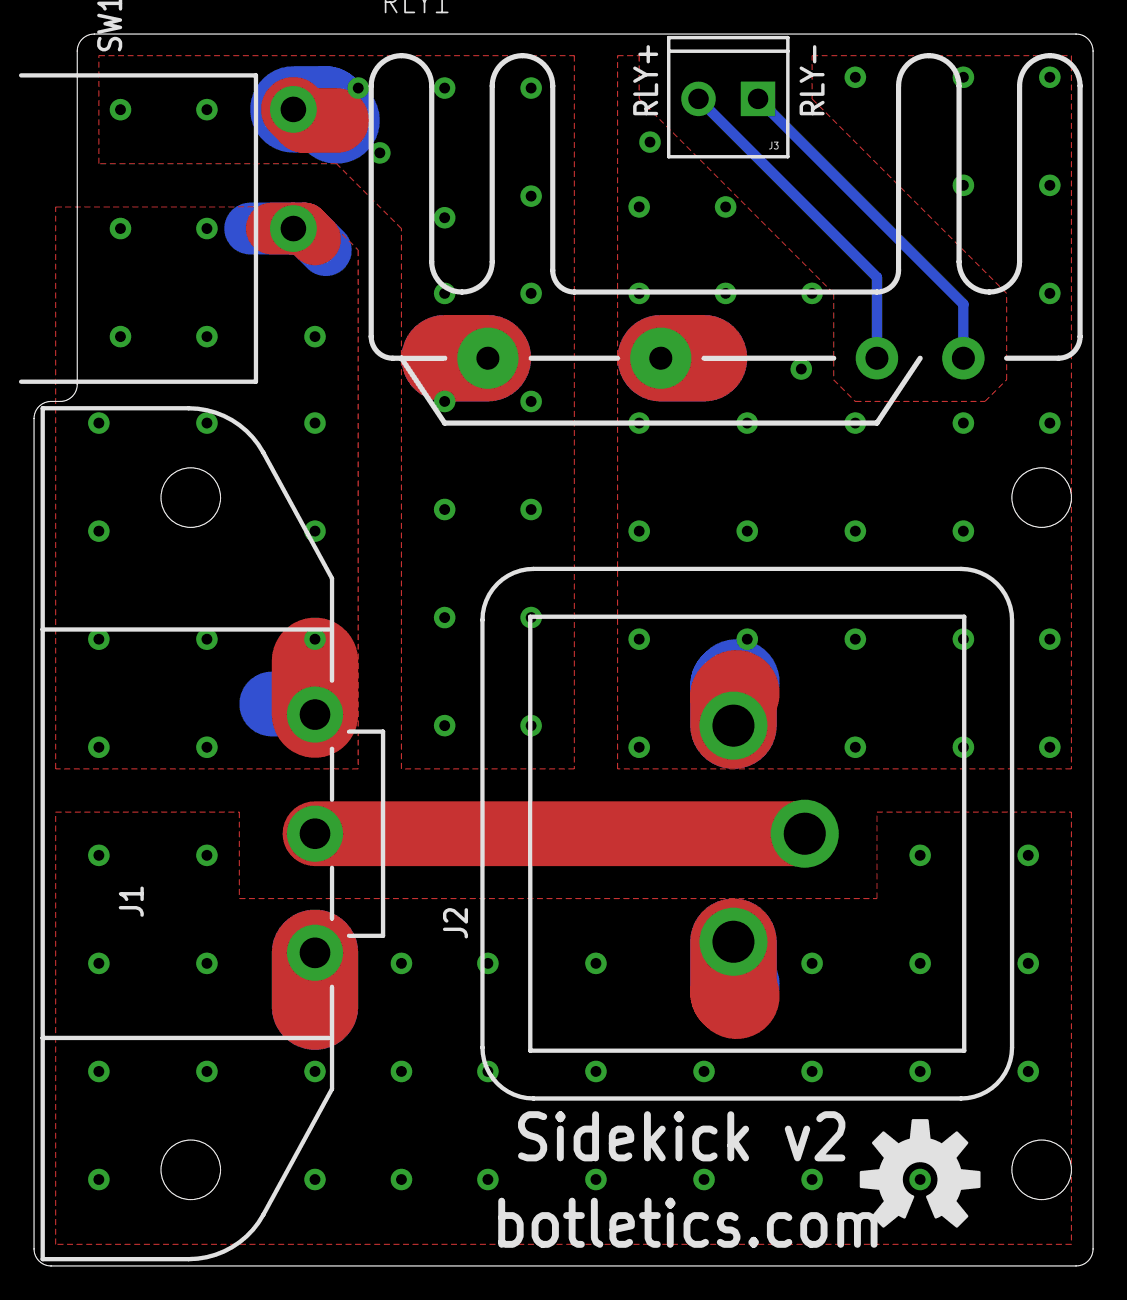
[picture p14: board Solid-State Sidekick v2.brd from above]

Board: 2 copper layers, 62.2 x 72.4 mm, 6 parts (0 on the bottom side), 7 nets.

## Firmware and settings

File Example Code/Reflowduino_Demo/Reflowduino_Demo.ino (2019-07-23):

/*
 * Title: Reflowduino Demo
 * Author: Timothy Woo
 * Website: www.botletics.com
 * Last modified: 7/23/2019
 * 
 * -----------------------------------------------------------------------------------------------
 * This is an example sketch for the Reflowduino reflow oven controller board. The default
 * settings in this code is for lead-free solder found in most solder paste, but the parameters
 * can be changed or added to suit your exact needs. The code implements temperature PID control
 * to follow the desired temperature profile and uses Bluetooth Low Energy (BLE) to communicate
 * the readings to the Reflowdiuno app. This code can also enable the Reflowduino to automatically
 * enter data points into Excel to graph the data in real time if connected to a computer. Simply
 * uncomment lines 262-268 to enable this feature!
 * 
 * Order a Reflowduino at https://www.botletics.com/products/reflowduino
 * Full documentation and design resources at https://github.com/botletics/Reflowduino
 * 
 * -----------------------------------------------------------------------------------------------
 * Credits: Special thanks to all those who have been an invaluable part of the DIY community,
 * like the author of the Arduino PID library and the developers at Adafruit!
 * 
 * -----------------------------------------------------------------------------------------------
 * License: This code is released under the GNU General Public License v3.0
 * https://choosealicense.com/licenses/gpl-3.0/ and appropriate attribution must be
 * included in all redistributions of this code.
 * 
 * -----------------------------------------------------------------------------------------------
 * Disclaimer: Dealing with mains voltages is dangerous and potentially life-threatening!
 * If you do not have adequate experience working with high voltages, please consult someone
 * with experience or avoid this project altogether. We shall not be liable for any damage that
 * might occur involving the use of the Reflowduino and all actions are taken at your own risk.
 */

#include <SoftwareSerial.h> // Library needed for Bluetooth communication
#include <Keyboard.h> // Only if you need the ATmega32u4 to act as a keyboard

// Libraries needed for using MAX31855 thermocouple interface
#include <SPI.h>
#include "Adafruit_MAX31855.h" // https://github.com/adafruit/Adafruit-MAX31855-library

// Library for PID control
#include <PID_v1.h> // https://github.com/br3ttb/Arduino-PID-Library

#include "pitches.h" // Includes the different notes for the buzzer

// Define pins
#define buzzer 5
#define relay 7
#define BT_RX 9
#define BT_TX 10
#define LED 13 // This LED is used to indicate if the reflow process is underway
#define MAX_CS 8 // MAX31855 chip select pin

// Initialize Bluetooth software serial
SoftwareSerial BT = SoftwareSerial(BT_TX,BT_RX); // Reflowduino (RX, TX), Bluetooth (TX, RX)

// Initialize thermocouple with hardware SPI
// Reflowduino uses hardware SPI to save digital pins
Adafruit_MAX31855 thermocouple(MAX_CS);

// Define if you want to enable the keyboard feature to type data into Excel
#define enableKeyboard false

// Define reflow temperature profile parameters (in *C)
// If needed, define a subtraction constant to compensate for overshoot:
#define T_const 5 // From testing, overshoot was about 5-6*C

// Standard lead-free solder paste (melting point around 215*C)
//#define T_preheat 150
//#define T_soak 217
//#define T_reflow 249 - T_const

// "Low-temp" lead-free solder paste (melting point around 138*C)
#define T_preheat 90
#define T_soak 138
#define T_reflow 165 - T_const

// Test values to make sure your Reflowduino is actually working
//#define T_preheat 50
//#define T_soak 80
//#define T_reflow 100 - T_const

#define T_cool 50 // Safe temperature at which the board is "ready" (dinner bell sounds!)
#define preheat_rate 2 // Increase of 1-3 *C/s
#define soak_rate 0.7 // Increase of 0.5-1 *C/s
#define reflow_rate 2 // Increase of 1-3 *C/s
#define cool_rate -4 // Decrease of < 6 *C/s max to prevent thermal shock. Negative sign indicates decrease

// Define PID parameters. The gains depend on your particular setup
// but these values should be good enough to get you started
#define PID_sampleTime 1000 // 1000ms = 1s
// Preheat phase
#define Kp_preheat 150
#define Ki_preheat 0
#define Kd_preheat 100
// Soak phase
#define Kp_soak 200
#define Ki_soak 0.05
#define Kd_soak 300
// Reflow phase
#define Kp_reflow 300
#define Ki_reflow 0.05
#define Kd_reflow 350

// Bluetooth app settings. Define which characters belong to which functions
#define dataChar '*' // App is receiving data from Reflowduino
#define stopChar '!' // App is receiving command to stop reflow process (process finished!)
#define startReflow 'A' // Command from app to "activate" reflow process
#define stopReflow 'S' // Command from app to "stop" reflow process at any time

double temperature, output, setPoint; // Input, output, set point
PID myPID(&temperature, &output, &setPoint, Kp_preheat, Ki_preheat, Kd_preheat, DIRECT);

// Buzzer settings
// This melody plays when the reflow temperature is reached,
// at which point you should open the door (for toaster ovens)
int openDoorTune[] = {
  NOTE_G6 // I found that NOTE_G6 catches my attention pretty well
};

// This melody plays at the very end when it's safe to take your PCB's!
int doneDealMelody[] = {NOTE_C4, NOTE_G3, NOTE_G3, NOTE_A3, NOTE_G3, 0, NOTE_B3, NOTE_C4};

// Note durations: 4 = quarter note, 8 = eighth note, etc.
int noteDurations[] = {4, 8, 8, 4, 4, 4, 4, 4};

// Logic flags
bool justStarted = true;
bool reflow = false; // Baking process is underway!
bool preheatComplete = false;
bool soakComplete = false;
bool reflowComplete = false;
bool coolComplete = false;

double T_start; // Starting temperature before reflow process
int windowSize = 2000;
unsigned long sendRate = 2000; // Send data to app every 2s
unsigned long t_start = 0; // For keeping time during reflow process
unsigned long previousMillis = 0;
unsigned long duration, t_final, windowStartTime, timer;

void setup() {
  Serial.begin(9600); // This should be different from the Bluetooth baud rate
  BT.begin(57600);

  pinMode(buzzer, OUTPUT);
  pinMode(LED, OUTPUT);
  pinMode(relay, OUTPUT);

  digitalWrite(LED, LOW);
  digitalWrite(relay, LOW); // Set default relay state to OFF

  myPID.SetOutputLimits(0, windowSize);
  myPID.SetSampleTime(PID_sampleTime);
  myPID.SetMode(AUTOMATIC); // Turn on PID control

//  while (!Serial) delay(1); // OPTIONAL: Wait for serial to connect
  Serial.println("*****Reflowduino demo*****");

  if (enableKeyboard) Keyboard.begin(); // Only if you want to type data into Excel
}

void loop() {
  /***************************** MEASURE TEMPERATURE *****************************/
  temperature = thermocouple.readCelsius(); // Read temperature
//  temperature = thermocouple.readFarenheit(); // Alternatively, read in deg F but will need to modify code
  
  /***************************** REFLOW PROCESS CODE *****************************/
  if (reflow) {
    digitalWrite(LED, HIGH); // Red LED indicates reflow is underway

    // This only runs when you first start the reflow process
    if (justStarted) {
      justStarted = false;
      
      t_start = millis(); // Begin timers
      windowStartTime = millis();
      T_start = temperature;
      
      if (isnan(T_start)) {
       Serial.println("Invalid reading, check thermocouple!");
      }
      else {
       Serial.print("Starting temperature: ");
       Serial.print(T_start);
       Serial.println(" *C");
      }
    }

    // Determine the amount of time that elapsed in any particular phase (preheat, soak, etc)
    duration = millis() - t_start;

    // Determine the desired set point according to where are in the reflow process
    // Perform a linear extrapolation of what desired temperature we want to be at.
    /********************* PREHEAT *********************/
    if (!preheatComplete) {
      if (temperature >= T_preheat) { // Check if the current phase was just completed
        preheatComplete = true;
        t_start = millis(); // Reset timer for next phase
        Serial.println("Preheat phase complete!");
      }
      else {
        // Calculate the projected final time based on temperature points and temperature rates
        t_final = (T_preheat - T_start) / (preheat_rate / 1000.0) + t_start; // Convert rate to *C/ms
        // Calculate desired temperature at that instant in time using linear interpolation
        setPoint = duration * (T_preheat - T_start) / (t_final - t_start);
      }
    }
    /********************* SOAK *********************/
    else if (!soakComplete) {
      if (temperature >= T_soak) {
        soakComplete = true;
        t_start = millis();
        Serial.println("Soaking phase complete!");
      }
      else {
        t_final = (T_soak - T_start) / (soak_rate / 1000.0) + t_start;
        setPoint = duration * (T_soak - T_start) / (t_final - t_start);
      }
    }
    /********************* REFLOW *********************/
    else if (!reflowComplete) {
      if (temperature >= T_reflow) {
        reflowComplete = true;
        t_start = millis();
        Serial.println("Reflow phase complete!");
        tone(buzzer, openDoorTune, 2000); // Alert the user to open the door!
      }
      else {
        t_final = (T_reflow - T_start) / (reflow_rate / 1000.0) + t_start;
        setPoint = duration * (T_reflow - T_start) / (t_final - t_start);
      }
    }
    /********************* COOLDOWN *********************/
    else if (!coolComplete) {
      if (temperature <= T_cool) {
        coolComplete = true;
        reflow = false;
        Serial.println("PCB reflow complete!");
        BT.print(stopChar); // Tell the app that the entire process is finished!
        playTune(doneDealMelody); // Play the buzzer melody
      }
      else {
        t_final = (T_cool - T_start) / (cool_rate / 1000.0) + t_start;
        setPoint = duration * (T_cool - T_start) / (t_final - t_start);
      }
    }

    // Use the appropriate PID parameters based on the current phase
    if (!soakComplete) myPID.SetTunings(Kp_soak, Ki_soak, Kd_soak);
    else if (!reflowComplete) myPID.SetTunings(Kp_reflow, Ki_reflow, Kd_reflow);
    
    // Compute PID output (from 0 to windowSize) and control relay accordingly
    myPID.Compute(); // This will only be evaluated at the PID sampling rate
    if (millis() - windowStartTime >= windowSize) windowStartTime += windowSize; // Shift the time window
    if (output > millis() - windowStartTime) digitalWrite(relay, HIGH); // If HIGH turns on the relay
//    if (output < millis() - windowStartTime) digitalWrite(relay, HIGH); // If LOW turns on the relay
    else digitalWrite(relay, LOW);
  }
  else {
    digitalWrite(LED, LOW);
    digitalWrite(relay, LOW);
  }

  /***************************** BLUETOOTH CODE *****************************/
  BT.flush();
  char request = ' ';

  // Send data to the app periodically
  if (millis() - previousMillis > sendRate) {
    previousMillis = millis();
    Serial.print("--> Temperature: "); // The right arrow means it's sending data out
    Serial.print(temperature);
    Serial.println(" *C");
    if (!isnan(temperature)) { // Only send the temperature values if they're legit
      BT.print(dataChar); // This tells the app that it's data
      BT.print(String(temperature)); // Need to cast to String for the app to receive it properly

      if (enableKeyboard && reflow) {
        // Type time and temperature data into Excel on separate columns!
        Keyboard.print((millis()-timer)/1000); // Convert elapsed time from ms to s
        Keyboard.print('\t'); // Tab to go to next column
        Keyboard.print(temperature);
        Keyboard.println('\n'); // Jump to new row
      }
    }
  }
  
  // Check for an incoming command. If nothing was sent, return to loop()
  if (BT.available() < 1) return;

  request = BT.read();  // Read request
//  Serial.print("REQUEST: "); Serial.println(request); // DEBUG

  if (request == startReflow) { // Command from app to start reflow process
    justStarted = true;
    reflow = true; // Reflow started!
    t_start = millis(); // Record the start time
    timer = millis(); // Timer for logging data points
    Serial.println("<-- ***Reflow process started!"); // Left arrow means it received a command
  }
  else if (request == stopReflow) { // Command to stop reflow process
    digitalWrite(relay, LOW); // Turn off appliance and set flag to stop PID control
    reflow = false;
    Serial.println("<-- ***Reflow process aborted!");
  }
  // Add you own functions here and have fun with it!

  /***************************** SERIAL COMM CONTROL *****************************/
  /*
  // Alternatively, read commands from the serial monitor
  char serialByte;
  
  if (Serial.available() > 0) {
    serialByte = Serial.read();
  }
  if (serialByte == startReflow) {
    justStarted = true;
    reflow = true; // Reflow started!
    t_start = millis(); // Record the start time
    timer = millis(); // Timer for logging data points
    Serial.println("<-- ***Reflow process started!"); // Left arrow means it received a command
  }
  else if (serialByte == stopReflow) { // Command to stop reflow process
    digitalWrite(relay, LOW); // Turn off appliance and set flag to stop PID control
    reflow = false;
    Serial.println("<-- ***Reflow process aborted!");
  }
  */
}

// This function plays the melody for the buzzer.
// Make this as simple or as elaborate as you wish!
void playTune(int *melody) {
  // Iterate over the notes of the melody:
  for (int thisNote = 0; thisNote < 8; thisNote++) {
    // To calculate the note duration, take one second divided by the note type
    // e.g. quarter note = 1000 / 4, eighth note = 1000/8, etc.
    int noteDuration = 1000 / noteDurations[thisNote];
    tone(buzzer, melody[thisNote], noteDuration);

    // To distinguish the notes, set a minimum time between them.
    // the note's duration + 30% seems to work well:
    int pauseBetweenNotes = noteDuration * 1.30;
    delay(pauseBetweenNotes);
    // stop the tone playing:
    noTone(buzzer);
  }
}

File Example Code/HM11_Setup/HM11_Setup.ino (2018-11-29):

/* This code configures the HM-11 Bluetooth module with a working baud rate
 *  and operating mode. It also changes the Bluetooth name from the default.
 *  
 *  See this page for a full list of AT commands: https://docs.google.com/document/d/14mHWT3GhELCj-6yxsam0k5bjzazq8nnPoz4B_gYh04k/edit#heading=h.lkl7kit1e1ct
 *  
 *  Author: Timothy Woo (botletics.com)
 *  Date: 10/4/2017
 */

#include <SoftwareSerial.h> // Library needed for Bluetooth communication

#define BT_RX 9
#define BT_TX 10

// Initialize Bluetooth software serial
SoftwareSerial BT(BT_TX,BT_RX); // Reflowduino (RX, TX), Bluetooth (TX, RX)

void setup() {
  Serial.begin(9600); // Should be different from Bluetooth baud
//  while (!Serial) {} // Wait for serial monitor to be opened
  
  BT.begin(115200); // HM-11 default baud rate, which isn't reliable
  delay(1); // This delay needs to be here in order to send the AT commands

  sendATcommand("AT+BOUD1", 1000); // Set to 57600 baud
  BT.begin(57600); // Need to use AT+BOUD1 command
  sendATcommand("AT+HOSTEN0", 1000); // Enable master/slave. Default is slave only.
  sendATcommand("AT+NAMEReflowduino", 1000); // Sets the Bluetooth name
}

void loop() {
  // Nothing here
}

void sendATcommand(String ATcommand, unsigned long timeout) {
  // Send AT command
  Serial.print("--> ");
  Serial.println(ATcommand);
  BT.print(ATcommand);

  // Print module's response without timeout
  Serial.print("<-- ");
  
  char c = ' ';
  unsigned long timer = millis(); // Start timer
  
  while (millis() - timer < timeout) {
    if (BT.available()) {
      char c = BT.read();
      Serial.print(c);
    }
  }
  
  if (c == ' ') Serial.println("\n"); // Print a new line if nothing was received
}

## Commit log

2017-10-21 Create Reflowduino Pro v2.sch
    [Reflowduino Pro v2.sch]
2017-10-21 Create Reflowduino Basic v2.sch
    [Reflowduino Basic v2.sch]
2017-10-26 Create Toasty Relay v1.sch
    [Toasty Relay v1.sch]
2017-10-26 Create Reflowduino Schematic.lol
2017-11-05 Create Solid-State Sidekick.sch
    [Solid-State Sidekick.sch]
2017-11-08 Added slot isolation at relay output
    [Reflowduino Pro v2.1.brd, Reflowduino Pro v2.1.sch]
2018-03-24 For ESP32 backpack
2018-10-17 Create Reflowduino Hackaday BOM v3.xlsx
    [Reflowduino Hackaday BOM v3.xlsx]
2019-06-17 Fix temperature rate conversion error
    [Reflowduino_Demo.ino]

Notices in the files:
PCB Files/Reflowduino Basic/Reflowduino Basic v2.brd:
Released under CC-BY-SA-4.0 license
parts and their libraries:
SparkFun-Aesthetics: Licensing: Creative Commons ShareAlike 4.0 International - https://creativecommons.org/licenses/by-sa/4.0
